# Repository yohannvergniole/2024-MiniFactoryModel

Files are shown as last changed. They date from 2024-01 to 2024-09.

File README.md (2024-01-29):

# Mini Factory Project

Template pour la création d'un repo type projet pour le MakerSpace. Doc gérée via le thème [Just-The-Docs](https://just-the-docs.com) en vanilla.

## Bienvenue sur Notre Projet

Ce repository est le cœur de notre projet. Ici, vous trouverez toutes les ressources nécessaires pour comprendre, utiliser et contribuer à notre projet.

### Contenu du Repository

- **Documentation :** Toutes les documentations techniques et guides d'utilisation sont disponibles dans le dossier `docs`. Voir le site de doc associé. 
- **project :** Toutes les sources de notre projet.

### Comment Utiliser ce Repository ?

- Pour commencer, consultez la documentation dans le dossier `docs`.
- Si vous souhaitez contribuer au projet, veuillez lire nos directives de contribution.

## Contribution

Nous accueillons et apprécions toute contribution. Si vous souhaitez contribuer, veuillez consulter notre guide de contribution pour connaître nos attentes et notre processus.

## Contact

Si vous avez des questions ou des suggestions, n'hésitez pas à nous contacter.

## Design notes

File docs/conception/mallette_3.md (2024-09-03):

---
layout: default
nav_order: 2
title: mallette 3
parent: Conception et prototypage
---

# Mallette 3

## Croquis

<script type="module" src="https://ajax.googleapis.com/ajax/libs/model-viewer/3.4.0/model-viewer.min.js"></script>

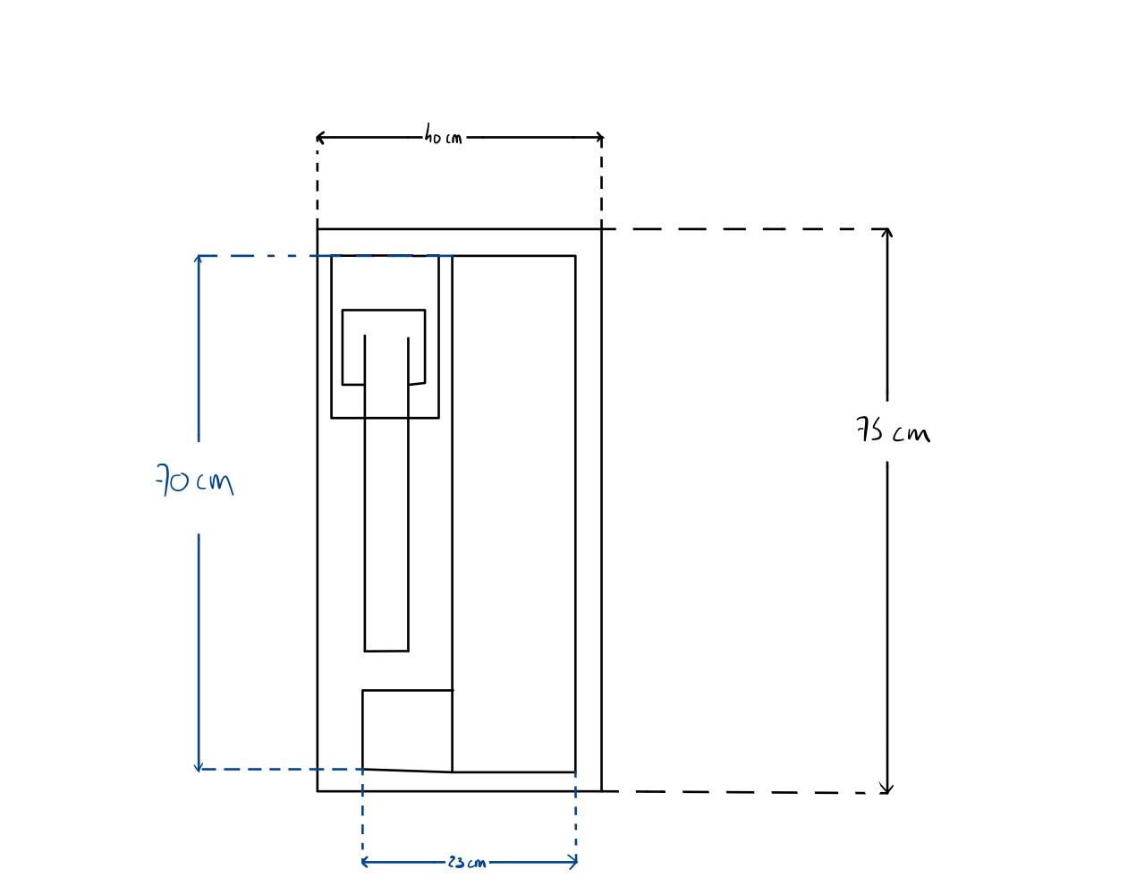
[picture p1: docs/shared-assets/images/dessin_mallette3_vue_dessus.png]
Plan de la mallette

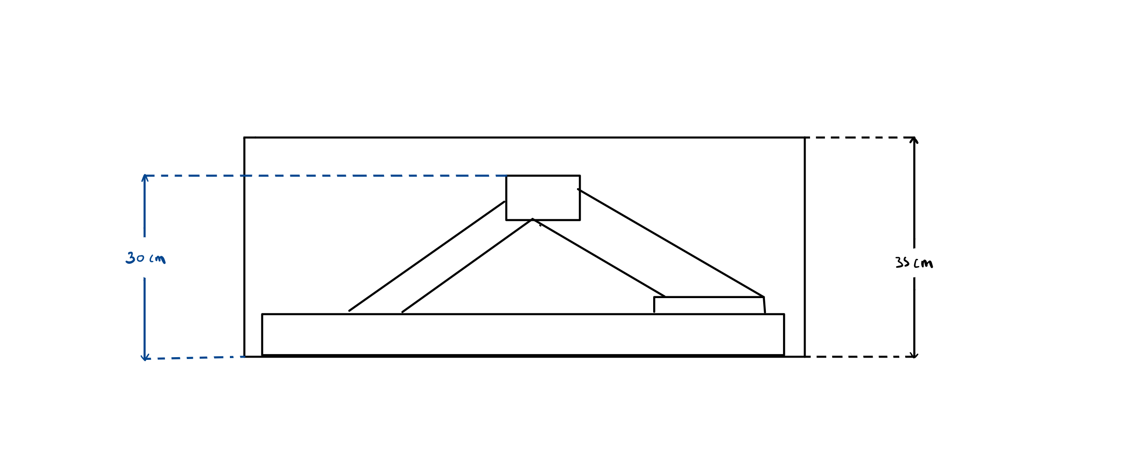
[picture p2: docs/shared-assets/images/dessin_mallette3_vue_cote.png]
Plan de la mallette

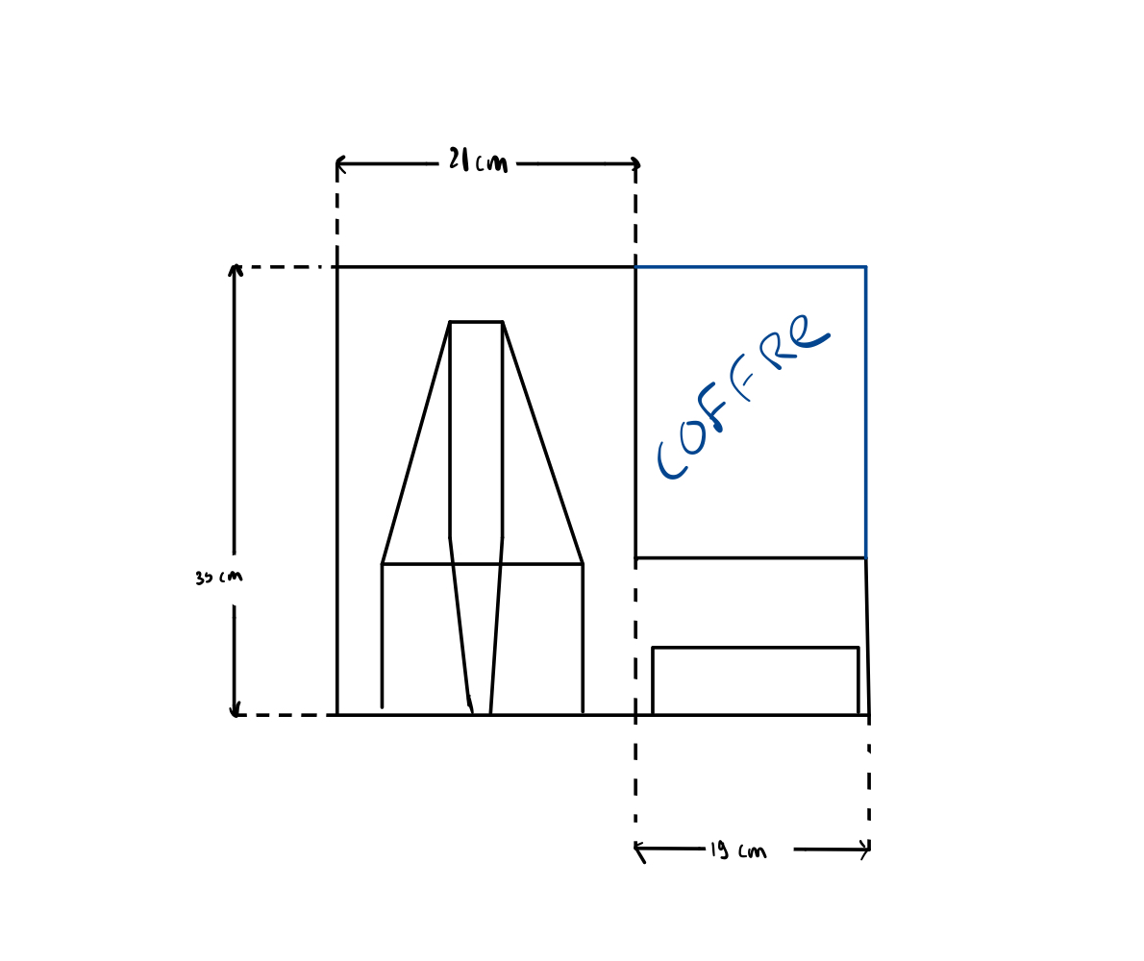
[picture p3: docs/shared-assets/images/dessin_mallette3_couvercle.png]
Plan de la mallette


---

## Modèle 3D

<model-viewer
    id="viewer"
    alt="Modèle 3D du bras robot Niryo Ned 2"
    src="../shared-assets/models/3D_REPRESENTATION.gltf"
    poster="../shared-assets/images/3D_REPRESENTATION.png"
    shadow-intensity="1"
    camera-controls
    touch-action="pan-z"
    rotation="0 0 90">
</model-viewer>

---

## Prototypage

Nous avons réalisé un prototype à l'échelle 1/10 des dimensions souhaitées pour le prototype final.
Ce prototype nous permettra d'éviter des erreurs futures lors de la conception. En effet, on a constaté qu'il manquait les coins sur les longueurs de la boîte.
On ajustera donc les dimensions du prototype final pour pouvoir obtenir un rectangle régulier.
Seul un côté restera sans coin, celui de la liaison des deux parties du socle puisque celles-ci doivent pouvoir s'aligner côte à côte.

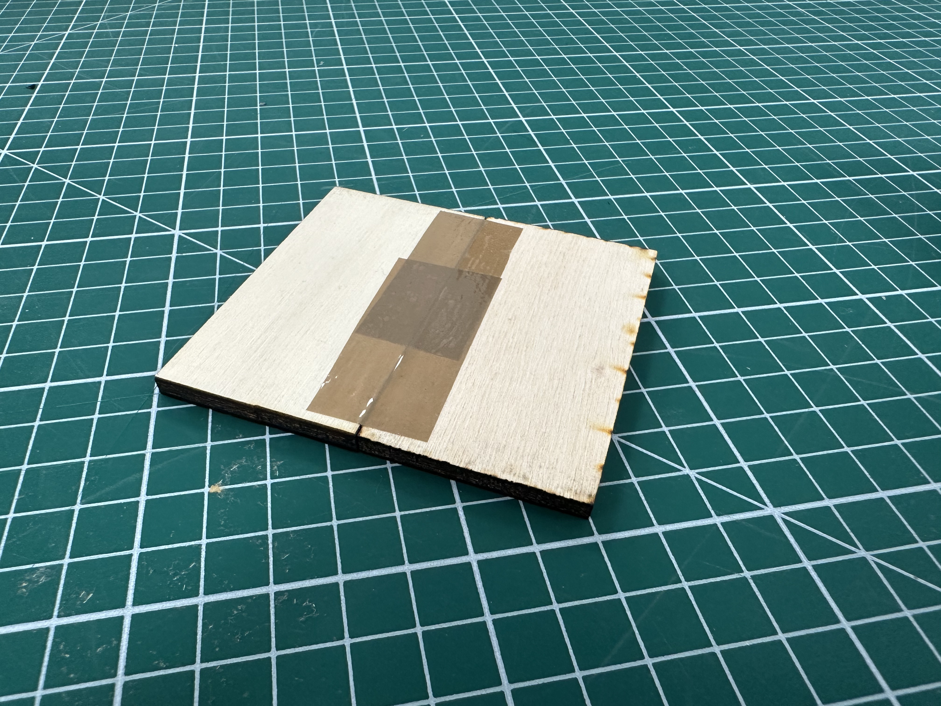
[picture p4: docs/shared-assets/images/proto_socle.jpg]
Photo socle

Photo du socle déplié, le scotch représente la charnière permettant la rotation des deux parties.

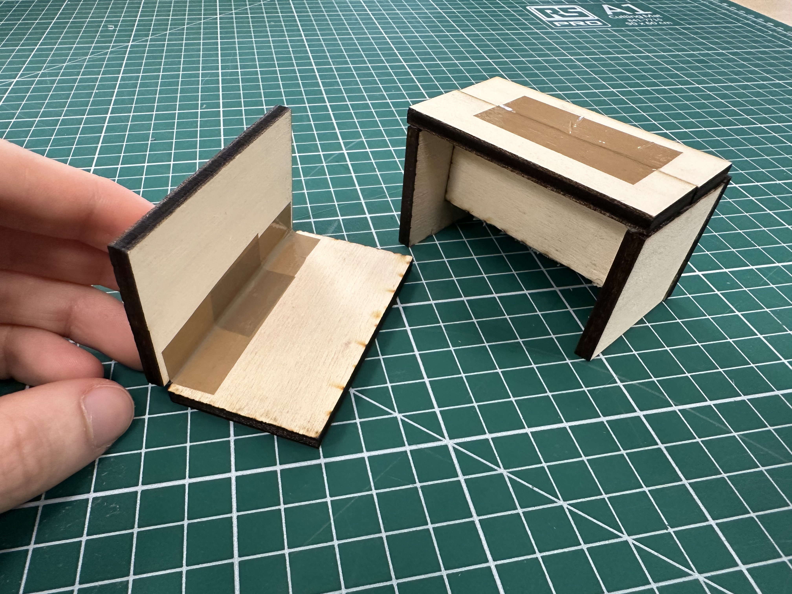
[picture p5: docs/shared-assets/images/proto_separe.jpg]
Photo socle et couvercle

Photo du socle et du couvercle séparé.

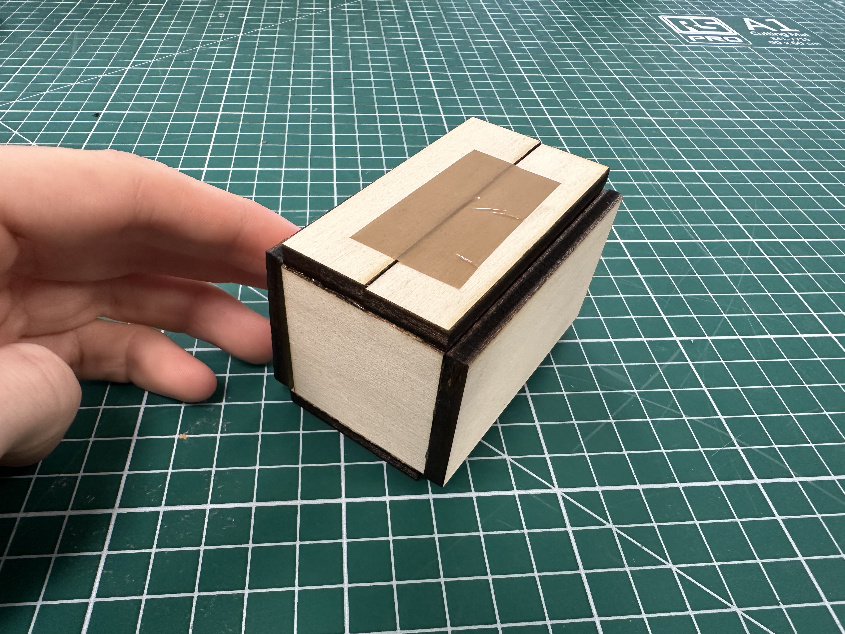
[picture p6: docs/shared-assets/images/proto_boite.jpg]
Photo boite

Photo de la boîte fermée lorsque le couvercle est posé sur le socle. Sur ce prototype, rien ne permet d'attacher le socle et le couvercle ensemble mais sur le prototype final ce sera fait grâce à des [sauterelles](../conception/supportCharniere.md).

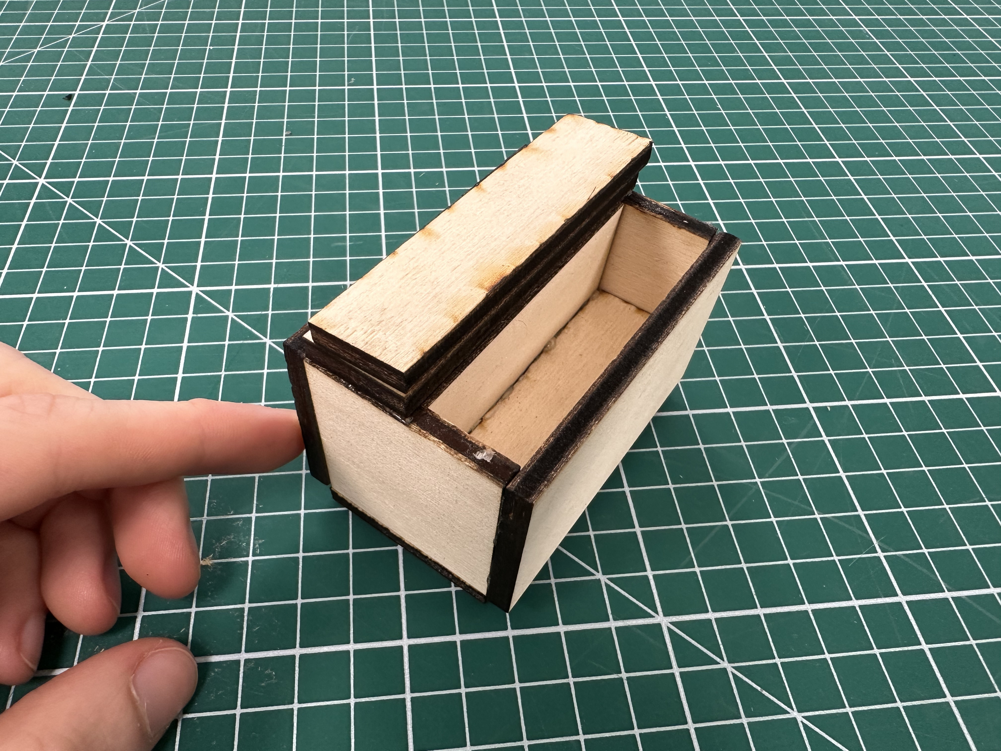
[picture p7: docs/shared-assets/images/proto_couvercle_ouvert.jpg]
Photo couvercle ouvert

Photo de la boîte avec le couvercle du coffre ouvert, ici aussi le scotch fais office de charnière.

<style>
    #viewer
    {
        margin : auto;
        width : 500px;
        height : 500px;
    }
</style>

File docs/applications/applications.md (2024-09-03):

---
layout: default
nav_order: 5
title: Modules
has_children: true
---

# Les différentes applications possibles avec notre Projet

Nous avons deux applications différentes.

La première est la simulation d'une chaîne de tri. Pour cette utilisation, nous pouvons utiliser un tri selon les couleurs et les formes. Il y a aussi la possibilité de choisir la couleur et la forme que nous souhaitons garder. [(voir page Module Chaine de Tri)](chaineTri.md)

La seconde est la prise d'un objet à un endroit précis et son transfert sur le convoyeur. [(voir page Module Transfert)](transfert.md)

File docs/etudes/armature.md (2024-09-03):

---
layout: default
nav_order: 7
title: Armature de la boîte
parent: Études et choix techniques
---
<script type="module" src="https://ajax.googleapis.com/ajax/libs/model-viewer/3.4.0/model-viewer.min.js"></script>

# Pourquoi une armature ?

Nous avons comme contrainte d'utiliser la découpeuse laser de l'école afin de réaliser notre mallette en planche de peuplier de 5mm. Cependant, avec la masse importante de matériel se trouvant dans la mallette, il est certain que des planches de 5mm ne suffieraient pas.
Nous avons étudié la possibilité de doubler l'épaisseur en réalisant la mallette avec deux couches de 5mm. La mallette était assez grande, cette possibilité nécessitait un nombre de planches conséquant. Pas le choix, nous avions besoin de trouver une alternative.
De cette conclusion résulte l'armature. En effet, une armature réalisé à partir de profilés de 20x20mm recouverte d'une planche de peuplier de 5mm semblait être la meilleure solution respectant nos contraintes.

<model-viewer
    id="viewer"
    alt="Modèle 3D de l'armature"
    src="../shared-assets/models/armature.gltf"
    poster="../shared-assets/images/capture_armature.png"
    shadow-intensity="1"
    camera-controls
    touch-action="pan-z"
    rotation="90 90 90">
</model-viewer>

<style>
    #viewer
    {
        margin : auto;
        width : 500px;
        height : 500px;
    }
</style>

Nous pouvons donc réaliser cette armature pour la base de la mallette ainsi que pour le côté accueillant le plateau des grilles modulaires. voir [mallette 3](../conception/mallette_3.html).

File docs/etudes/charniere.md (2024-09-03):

---
layout: default
nav_order: 8
title: Charnière
parent: Études et choix techniques
---

<script type="module" src="https://ajax.googleapis.com/ajax/libs/model-viewer/3.4.0/model-viewer.min.js"></script>

Étant donné que nous avons besoin qu'un côté de la mallette soit pliable, nous avons besoin d'un mécanisme permettant de le faire. Nous avons donc opté pour une charnière piano sur toute la longueur de la mallette.

<model-viewer
    class="viewer"
    alt="Modèle 3D de l'armature"
    src="../shared-assets/models/hinge.gltf"
    poster="../shared-assets/images/capture_charniere.png"
    shadow-intensity="1"
    camera-controls
    touch-action="pan-z"
    rotation="90 90 90">
</model-viewer>

<style>
    .viewer
    {
        margin : auto;
        width : 500px;
        height : 500px;
    }
</style>

Nous pouvons ainsi la fixer sur notre mallette. Cependant, cette charnière nous inflige une nouvelle contrainte. En effet, à cause de celle-ci, nous ne pouvons pas fixer notre armature sur les bords de nos planches de peuplier : les profilés faisant 20mm et la charnière faisant 32mm (donc 16mm de chaque côté), il est impossible de fixer notre charnière sur nos planches. Nous avons donc décider de décaler l'armature comme ceci :
<model-viewer
    class="viewer"
    alt="Modèle 3D de l'armature"
    src="../shared-assets/models/problemeCharniere.gltf"
    poster="../shared-assets/images/problemeCharniere.png"
    shadow-intensity="1"
    camera-controls
    touch-action="pan-z"
    rotation="90 90 90">
</model-viewer>

Malheureusement pour nous, ceci créé un autre problème. Visser la charnière seulement dans une plaque de 5mm met en péril la solidité de la structure. Nous avons donc besoin d'une [pièce de support](../realisation/ressources.md#les-profilés) dans laquelle nous allons visser la charnière.

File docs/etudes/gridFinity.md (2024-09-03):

---
layout: default
nav_order: 4
title: Projet Gridfinity
parent: Études et choix techniques
---

# Projet GridFinity

Le projet GridFinity est un système de rangement générique à imprimer en 3D. Il permet à n'importe qui de créer sa structure de rangement selon ses propres besoins.
Le principe est simple et similaire à celui des legos, on modélise des blocs de différentes tailles basés sur le même pattern afin de les emboîter facilement.
Voici des exemples afin de mieux comprendre le principe :

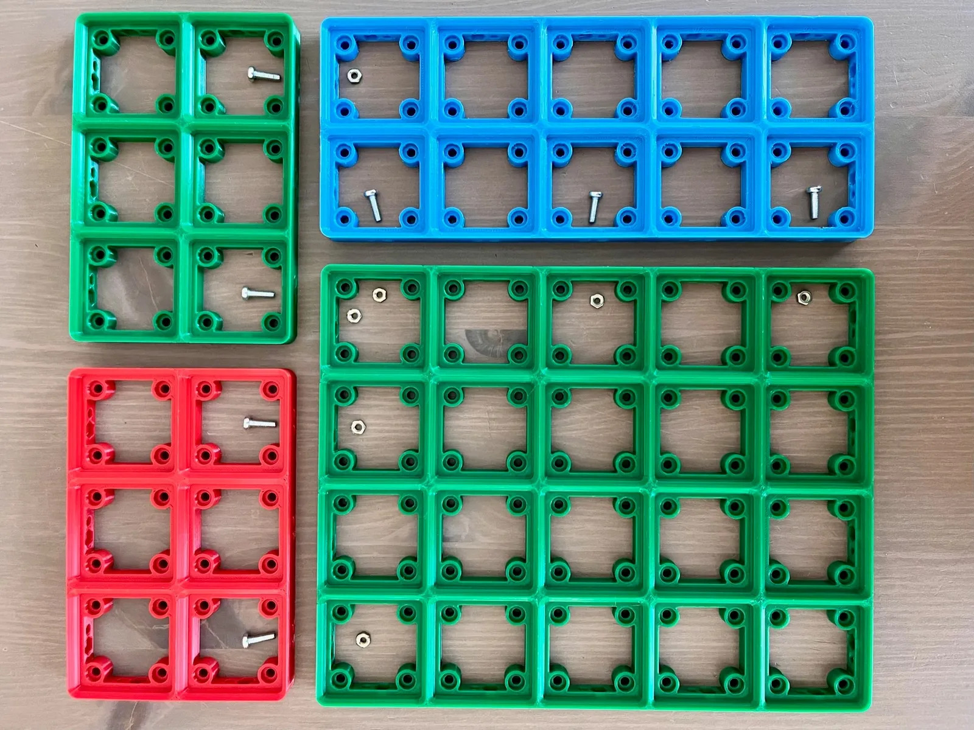
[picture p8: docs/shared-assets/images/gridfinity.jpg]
Illustration du projet gidfinity

*Sources :*
*[https://www.printables.com/fr/model/500544-gridfinity-baseplate-screwable/user-gcodes](https://www.printables.com/fr/model/500544-gridfinity-baseplate-screwable/user-gcodes)*

*[https://gridfinity.xyz](https://gridfinity.xyz)*

## Utilisation dans notre projet

Nous voulons utiliser ce système dans notre projet afin de faciliter la modularité. Ce système nous offre de nombreuses possibilités comme le fait de faire un plateau à coordonnées par exemple.

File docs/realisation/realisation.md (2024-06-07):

---
layout: default
title: Réalisation
nav_order: 7
has_children: true
---

# Étapes de Réalisation

Bienvenue dans la section dédiée aux étapes de fabrication du projet mini usine. Ici, vous trouverez des guides détaillés pour chaque étape du processus de fabrication.

## Sommaire des Étapes

Le processus de fabrication est divisé en plusieurs étapes clés :

1. [Choix des matériaux](ressources.md)
2. [Assemblage](assemblage.md)

---

Pour toute question ou aide supplémentaire, n'hésitez pas à contacter notre équipe.

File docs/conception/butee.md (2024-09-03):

---
layout: default
nav_order: 3
title: Butée 
parent: Conception et prototypage
---

## Première tentative

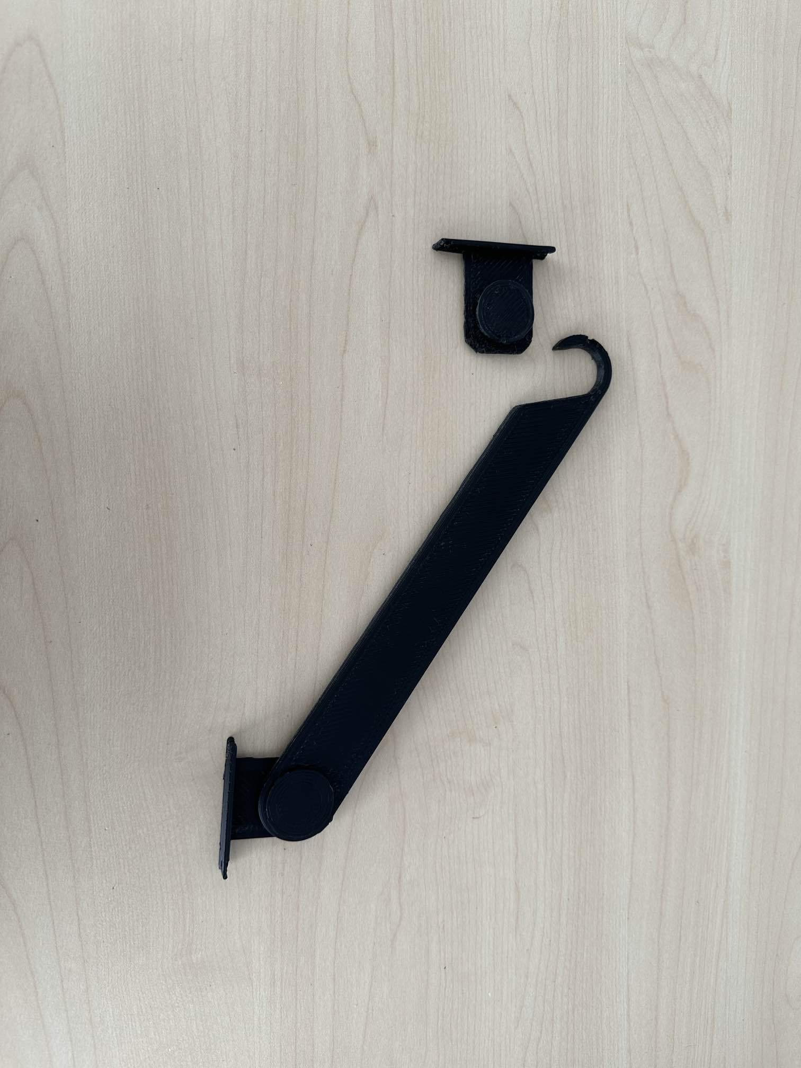
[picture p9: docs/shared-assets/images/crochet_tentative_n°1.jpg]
Illustration crochet tentative n°1


Notre crochet était malheureusement trop long pour qu'il puisse se glisser sur le support que l'on peut voir sur l'image ci-dessus.
De plus, certaines liaisons n'ont pas été parfaitement dimensionnées, nous avonc dû ajuster le tir sur la seconde tentative afin d'obtenir un glissement parfait et un bon maintien des cotés de la mallette lors de sa fermeture par le biais des crochets.

## Seconde tentative

Illustration crochet tentative finale

Sur cette itération finale, nous avons pris la décision de faire un crochet allongé avec un creux parrallèle à la plaque inférieure de la mallette afin de faciliter l'emboîtement des deux pièces tout en s'assurant du maintien de la plaque latérale.

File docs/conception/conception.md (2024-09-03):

---
layout: default
nav_order: 6
title: Conception et prototypage
has_children: true
---

# Conception et prototypage

Nous avons imaginé 3 possibilités pour réaliser notre projet.
Ci-dessous nous vous présentons les modèles 3D des différentes idées en expliquant pour chaque leurs avantages et leurs inconvénients.

## Mallette 1

<script type="module" src="https://ajax.googleapis.com/ajax/libs/model-viewer/3.4.0/model-viewer.min.js"></script>

<model-viewer
    id="viewer"
    alt="Modèle 3D du bras robot Niryo Ned 2"
    src="../shared-assets/models/mallette_1.gltf"
    poster="../shared-assets/images/capture_niryo.jpg"
    shadow-intensity="1"
    camera-controls
    touch-action="pan-z"
    rotation="0 0 90">
</model-viewer>

<style>
    #viewer
    {
        margin : auto;
        width : 500px;
        height : 500px;
    }
</style>

| Avantages | Inconvénients |
| :---: | :---: |
| Tout est contenu dans la boîte  | Volumineuse |
|  | Transport |

## Mallette 2

<model-viewer 
    id="viewer"
    alt="Modèle 3D du bras robot Niryo Ned 2"
    src="../shared-assets/models/mallette_2.gltf"
    poster="../shared-assets/images/capture_niryo.jpg"
    shadow-intensity="1"
    camera-controls
    touch-action="pan-z"
    rotation="0 0 90">
</model-viewer>

| Avantages | Inconvénients |
| :---: | :---: |
| Tout est contenu dans la boîte  | Instable |
|  | Descente du bras robot restreinte |

## Mallette 3

<model-viewer
    id="viewer"
    alt="Modèle 3D du bras robot Niryo Ned 2"
    src="../shared-assets/models/3D_REPRESENTATION.gltf"
    poster="../shared-assets/images/3D_REPRESENTATION.png"
    shadow-intensity="1"
    camera-controls
    touch-action="pan-z"
    rotation="0 0 90">
</model-viewer>

| Avantages | Inconvénients |
| :---: | :---: |
| Tout est contenu dans la boîte  | Encombrant à transporter |
| Plan de travail réduit |  |

C'est ce choix que nous avons décidé de réaliser.

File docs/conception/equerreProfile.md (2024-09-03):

---
layout: default
nav_order: 5
title: Equerre Profilés
parent: Conception et prototypage
---

L'équerre pour profilé a été modélisée et imprimée en 3D pour assurer le maintien de l'armature réalisée avec les profilés.
Nous avons décidé de les réaliser nous-mêmes pour gagner du temps et limiter les dépenses, car une équerre en impression 3D coûte moins cher qu'une réalisée en métal.

<script type="module" src="https://ajax.googleapis.com/ajax/libs/model-viewer/3.4.0/model-viewer.min.js"></script>

<model-viewer
    id="viewer"
    alt="Modèle 3D du bras robot Niryo Ned 2"
    src="../shared-assets/models/equerreFixe.gltf"
    poster="../shared-assets/images/equerreFixe.png"
    shadow-intensity="1"
    camera-controls
    touch-action="pan-z"
    rotation="90 90 90">
</model-viewer>

<style>
    #viewer
    {
        margin : auto;
        width : 500px;
        height : 500px;
    }
</style>

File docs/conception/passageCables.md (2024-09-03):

---
layout: default
nav_order: 6
title: Passage de  Câbles
parent: Conception et prototypage
---
<script type="module" src="https://ajax.googleapis.com/ajax/libs/model-viewer/3.4.0/model-viewer.min.js"></script>

Afin d'organiser l'espace de travail de notre mini usine, nous avons décidé de réaliser des passages de câbles. Cela évite que le robot ne s'emmêle dans les câbles et nous permet en même temps d'avoir un espace de travail rangé et agréables à utiliser.
Cette pièce montre également l'étendue des possibilités que nous avons grâce à la grille modulaire.

<model-viewer 
    id="viewer" 
    alt="Support Charnière" 
    src="../shared-assets/models/passageCables.gltf" 
    poster="../shared-assets/images/passageCables.png" 
    shadow-intensity="1" 
    camera-controls 
    touch-action="pan-z"
    rotation="90 90 90">
</model-viewer>

<style>
    #viewer
    {
        margin : auto;
        width : 500px;
        height : 500px;
    }
</style>

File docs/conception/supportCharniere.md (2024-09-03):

---
layout: default
nav_order: 4
title: Support de la charnière
parent: Conception et prototypage
---

Ce support modélisé en 3D permet de fixer la charnière au socle.
Nous avons réalisé une pièce qui se glisse dans le profilé, ce qui facilite la fixation nécessitant une vis et un écrou. Nous l'avons modélisé en 3D car nous voulions une forme spécifique pour notre projet, non disponible sur le marché.

<script type="module" src="https://ajax.googleapis.com/ajax/libs/model-viewer/3.4.0/model-viewer.min.js"></script>

<model-viewer 
    id="viewer" 
    alt="Support Charnière" 
    src="../shared-assets/models/SUP_CHARNIERE.gltf" 
    poster="../shared-assets/images/SUP_CHARNIERE.png" 
    shadow-intensity="1" 
    camera-controls 
    touch-action="pan-z"
    rotation="90 90 90">
</model-viewer>

<style>
    #viewer
    {
        margin : auto;
        width : 500px;
        height : 500px;
    }
</style>

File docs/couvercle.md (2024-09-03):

---
layout: default
nav_order: 10 
title: Modèle 3D du couvercle
---

<script type="module" src="https://ajax.googleapis.com/ajax/libs/model-viewer/3.4.0/model-viewer.min.js"></script>

# Modèle 3D du couvercle

Nous avons modélisé le couvercle, si vous souhaitez le réaliser vous pouvez voir un aperçu ci-dessous. 
Le fichier est disponible dans les ressources du site.

<model-viewer
    id="viewer"
    alt="Modèle 3D du couvercle"
    src="../shared-assets/models/couvercle.gltf"
    poster="../shared-assets/images/couvercle.png"
    shadow-intensity="1"
    camera-controls
    touch-action="pan-z"
    rotation="90 90 90">
</model-viewer>

<style>
    #viewer
    {
        margin : auto;
        width : 500px;
        height : 500px;
    }
</style>

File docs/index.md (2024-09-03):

---
layout: home
nav_order: 1
title: Accueil
---

# Bienvenue sur notre documentation du projet Mini Factory

Bienvenue dans la documentation du projet Mini Factory Model. Ce site a pour but de fournir toutes les informations nécessaires pour comprendre, utiliser et reproduire efficacement notre projet.

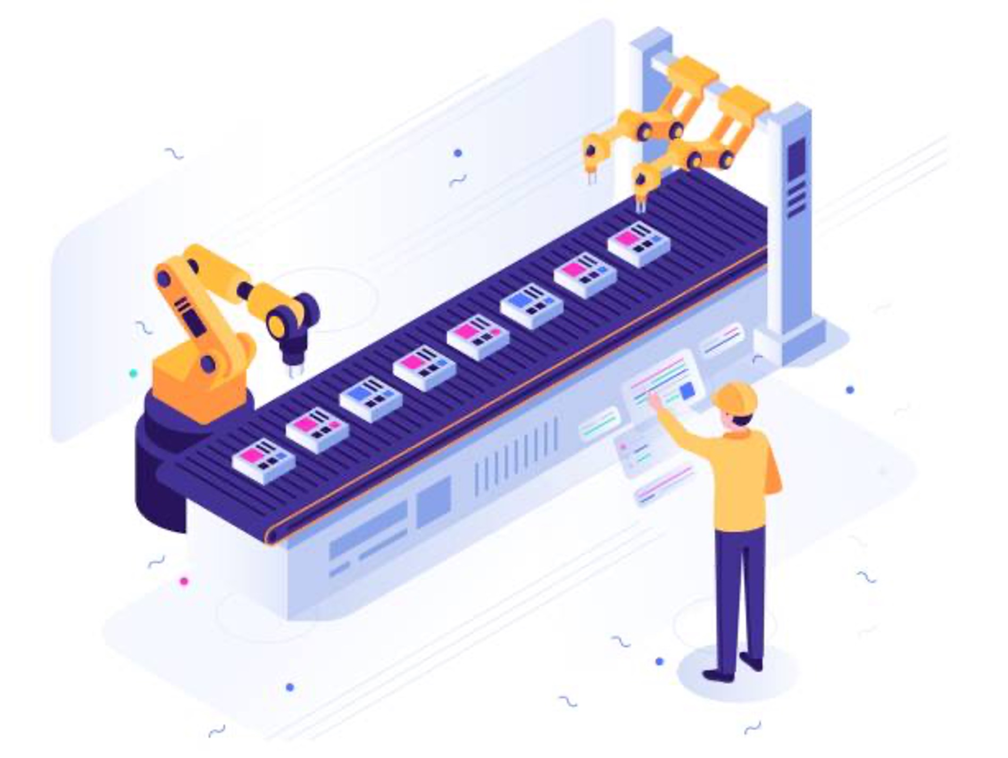
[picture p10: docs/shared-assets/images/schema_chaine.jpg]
Illustration montrant un schéma d'une chaîne représantant notre projet de maquette d'intéraction sur des objets présent sur un convoyeur


## À propos du Projet

Le but principal de la chaîne de production est de trier des objets en fonction des formes et/ou des couleurs en utilisant le bras robotisé.

Le but de notre projet est de réaliser une maquette de chaîne de tri transportable vers diverses lieux. En effet, Unilasalle Amiens possède une filière PAUC (Production Automatisée et Usine Connectée) et un tel projet, pourrait permettre de faire la promotion de cette filière ou simplement de faire découvrir l’univers de l'industrie et de la production automatisée.

## Poster

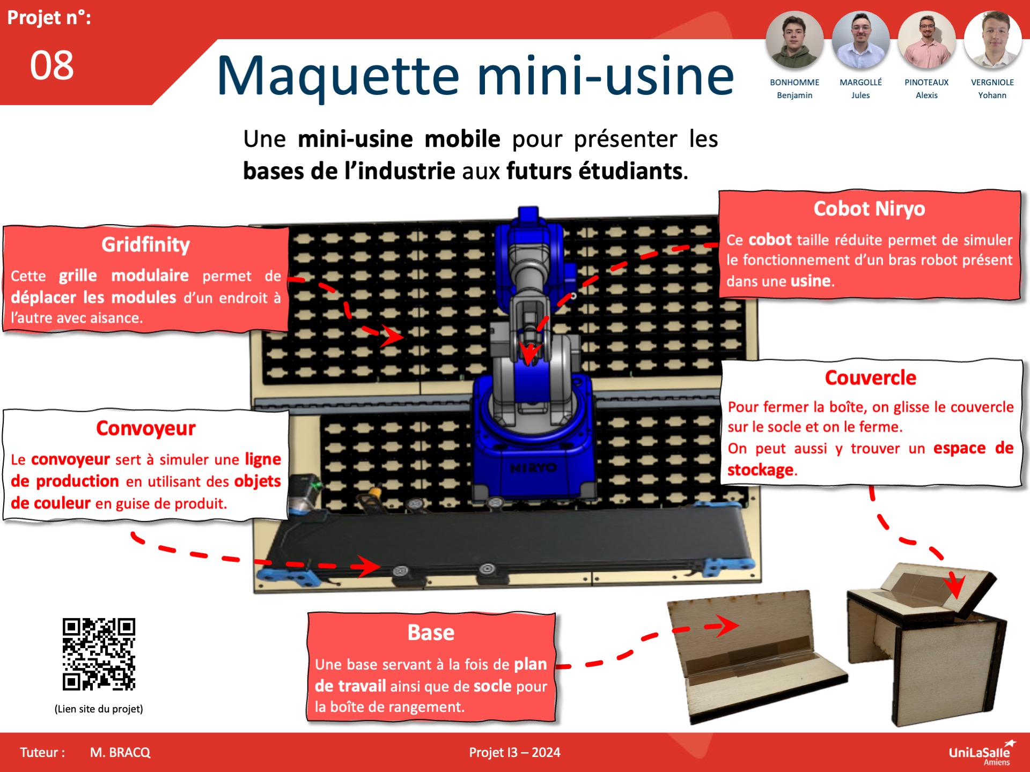
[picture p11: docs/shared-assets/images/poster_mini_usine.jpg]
photo poster


## Vidéo

<iframe width="100%" height="500" src="https://www.youtube.com/embed/1ccF_rse7Ak" frameborder="0" allow="accelerometer; autoplay; encrypted-media; gyroscope; picture-in-picture" allowfullscreen></iframe>

---

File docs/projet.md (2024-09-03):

---
layout: default
nav_order: 3 
title: Présentation du projet
---

# Présentation du projet

## Introduction

Dans le cadre de notre projet I3, nous avons à réaliser un projet sur 75h de cours sans compter le temps personnel à investir. Ce projet à pour objectif de développer le travail en équipe sur des sujets en cohérence avec les études et les compétences que l'on souhaite développer ultérieurement.

## Contexte du Projet

Plusieurs sorties promotionnelles sont organisées par le pôle communication de l'école dans les alentours d'Amiens afin d'attirer de nouveaux élèves. Celles-ci ont pour objectif de promouvoir au mieux les compétences développées au sein de l'école de manière simple et ludique. Notre projet est né de ce postulat de base, la nécessité de créer un support visuel et physique qui puisse exposer du mieux possible les connaissances et l'expertise transmisent dans notre cursus scolaire.

## Objectifs du Projet

Nous nous sommes orientés sur ce projet dans le but de fournir une maquette/chaîne robotique de production concrète miniaturisée et transportable. Celle-ci a comme objectif d'être facile à prendre en main et à installer pour l'utilisateur et pour ceux qui observent. Cette chaine de production sera modulable afin de promouvoir la polyvalence de l'enseignement avec une maquette multi-usage.

## Cahier des Charges

[https://cloudlasalle-my.sharepoint.com/:x:/g/personal/alexis_pinoteaux_etu_unilasalle_fr/Ee9_swYYa1JEvp3mi1WHuzgBoHQftADFWFV2qyiBQeqNow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)](https://cloudlasalle-my.sharepoint.com/:x:/g/personal/alexis_pinoteaux_etu_unilasalle_fr/Ee9_swYYa1JEvp3mi1WHuzgBoHQftADFWFV2qyiBQeqNow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)

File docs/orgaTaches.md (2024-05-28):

---
layout: default
nav_order: 9 
title: Organisation des Tâches
---
# Organisation des Tâches

Afin d'organiser notre travail, nous avons choisi de créer un tableau Trello utilisant la méthode Kanban. Cette méthode nous permet une bonne visualisation des tâches à effectuer et facilite la répartition.

<embed type="text/html" src="https://trello.com/b/otUl7l00.html" width="800" height="600">
[Lien vers le Trello](https://trello.com/b/otUl7l00/mini-factory)

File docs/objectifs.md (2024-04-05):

---
layout: default
nav_order: 2
title: Maquette de chaîne de production 
---

# Introduction

Dans le cadre de notre projet I3, nous avons à réaliser un projet sur 75h de cours sans compter le temps personnel à investir pour développer le travail en équipe sur des sujets en cohérence avec les études et les compétences que l'on souhaite développer ultérieurement.

# Contexte du Projet

Plusieurs sorties promotionnelles sont organisées par le pôle communication de l'école dans les alentours d'amiens afin d'attirer de nouveaux élèves. Celles-ci ont pour objectif de promouvoir au mieux les compétences développées au sein de l'école de manière simple et ludique. Notre projet est né de ce postulat de base, la nécessité de créer un support visuel et physique qui puisse exposé du mieux possible les connaissances et l'expertise transmise dans notre cursus scolaire.

# Objectifs du Projet

Nous nous sommes orientés sur ce projet dans le but de fournir une maquette/chaîne robotique de production concrète miniaturisée et transportable. Celle-ci a comme objectif d'être facile à prendre en main et à installer pour l'utilisateur et pour ceux qui observent. Cette chaine de production sera modulable afin de promouvoir la polyvalence de l'enseignement avec une maquette multi-usage.

# Existant

Nous avons repris l'idée originale de ce projet qui a été trouvée lors du projet I2 sur un autre bras. Pour parvenir à un résultat concluant, nous partons d'un bras robotisé le ned 2 qui est fourni par l'école au début de ce projet avec ses accessoires.

# Cahier des Charges

[https://cloudlasalle-my.sharepoint.com/:x:/g/personal/alexis_pinoteaux_etu_unilasalle_fr/Ee9_swYYa1JEvp3mi1WHuzgBoHQftADFWFV2qyiBQeqNow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)](https://cloudlasalle-my.sharepoint.com/:x:/g/personal/alexis_pinoteaux_etu_unilasalle_fr/Ee9_swYYa1JEvp3mi1WHuzgBoHQftADFWFV2qyiBQeqNow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)

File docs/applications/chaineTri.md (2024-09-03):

---
layout: default
nav_order: 2
title: Module Chaine de tri
parent: Modules
---

# Chaîne de Tri

Cette application est la première idée que nous avons eu en commençant le projet.

## Fonctionnement

L'utilisateur doit d'abord placer le robot à l'emplacement lié à la démonstration comme ci-dessous.

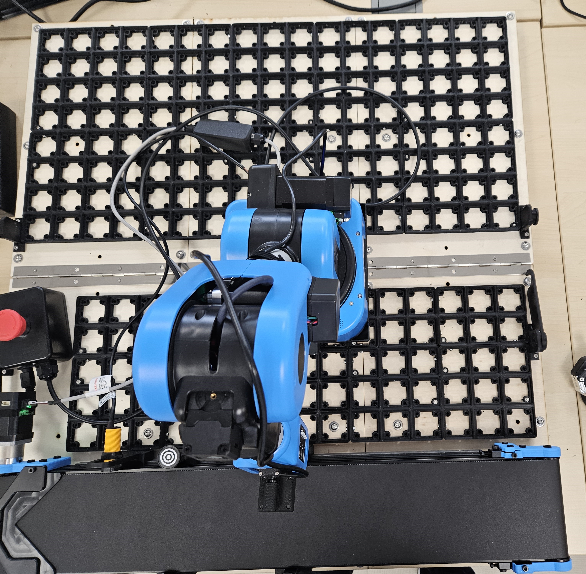
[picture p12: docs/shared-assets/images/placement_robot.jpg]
photos montrant le placement robot


Par la suite, il faut placer les 3 plaques qui recevront les objets triés.

## Matériel

Pour ce module, nous avons besoin :

- Un convoyeur qui va amener les objets au bras robot
- Le bras robot
- Des capteurs pour la couleur et la forme des objets
- Des plaques pour recevoir les objets triés

## Le kit Vision de Niryo

Niryo met en vente beaucoup d'accessoires pouvant compléter le bras robot, parmi ceux-ci, nous retrouvons le kit Vision.

animation gif du kit vision de niryo

<br>

Le kit Vision nous permet de faire de la reconnaissance de forme et de couleur, parfait pour notre module.
Nous utiliserons uniquement les trois couleurs des objets fournis (rouge, vert et bleu) ainsi que leurs deux formes utilisées (rond et carré).
Le kit vision comprend :

- Une zone de travail
- Une caméra
- Des objets à manipuler
- Une pointe de précision

La zone de travail est une zone créée par 4 "balises" permettant à la caméra de se repérer.

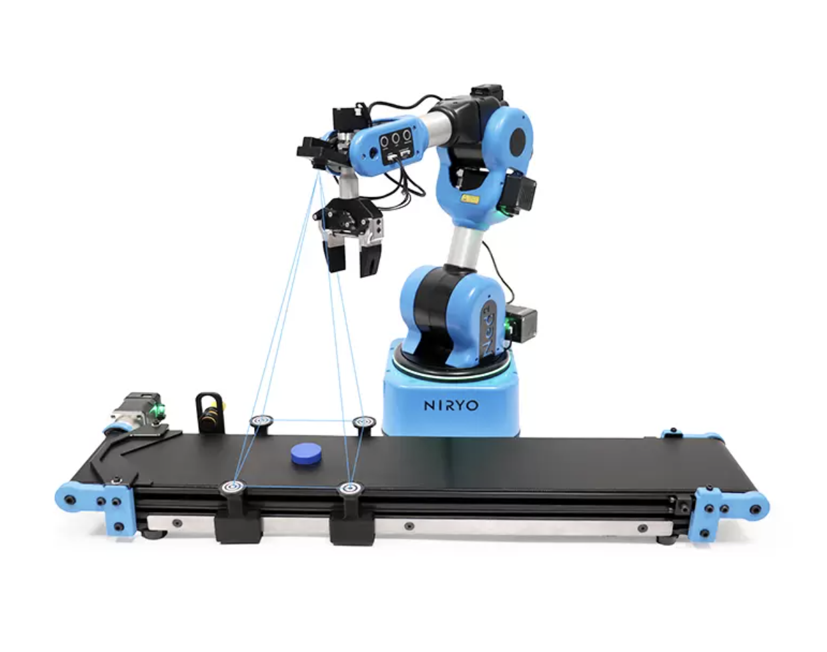
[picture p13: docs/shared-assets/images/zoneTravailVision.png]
image de la zone de travail du kit vision


## Et après le tri ?

L'utilisateur renseigne donc la façon dont il veut trier ses objets et le bras fait tout le reste. Les objets lui sont amenés via un convoyeur et il les range ensuite dans leur boîte attitrée.
Par exemple, si l'utilisateur veut trier les objets par couleur et ne garder que la couleur <span style="color:green;">verte</span>, alors il aura besoin de deux contenant : un pour les objets verts, et un pour le reste.

*Source : https://niryo.com/fr/produits-cobots/ensemble-de-vision-ned2/*

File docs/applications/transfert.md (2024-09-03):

---
layout: default
nav_order: 3
title: Module Transfert 
parent: Modules
---

# Transfert de prièce

## Fonctionnement

L'utilisateur doit d'abord placer le robot à l'emplacement lié à la démonstration comme ci-dessous.

photos montrant le placement robot

Par la suite, il faut placer la plaque qui recevra les objets à transporter.

Une fois le programme lancé, les objets devront être placés les uns après les autres pendant l'execution du programme. Il faut faire attention à bien placer la pièce au centre de la plaque.

## Matériel

Pour ce module, nous avons besoin :

- Un convoyeur qui va amener les objets au bras robot
- Le bras robot
- Une plaque pour prendre les objets

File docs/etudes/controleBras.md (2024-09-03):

---
layout: default
nav_order: 6
title: Contrôle du Bras
parent: Études et choix techniques
---

# Comment contrôler le bras Niryo ?

Nous pouvons contrôler le bras robot grâce à un logiciel disponible gratuitement et conçu spécialement pour l'utilisation du bras.

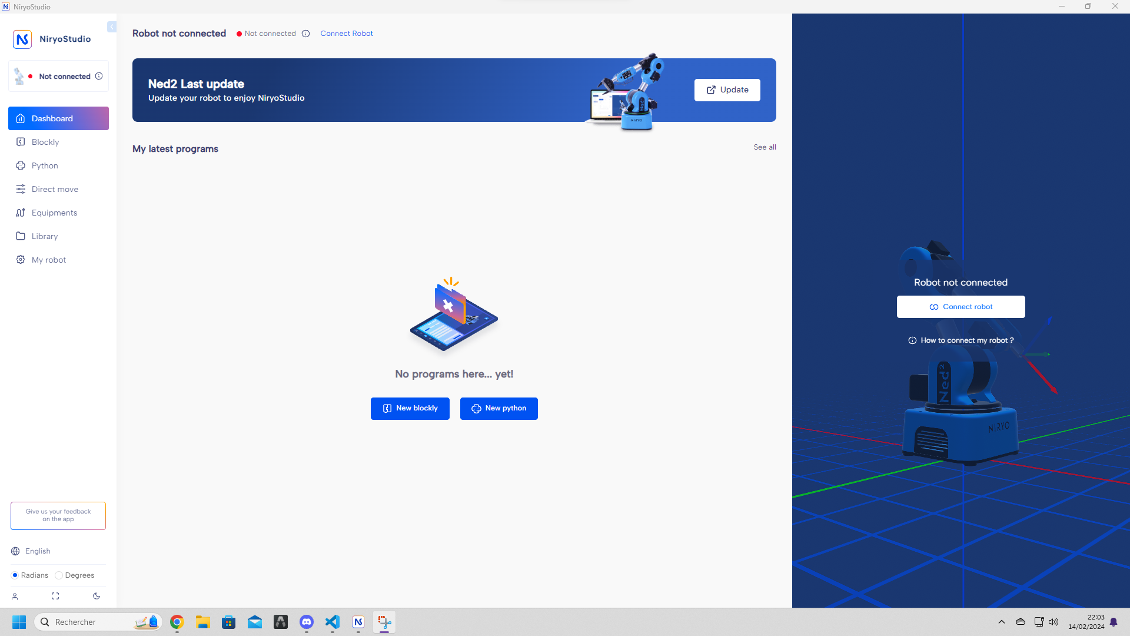
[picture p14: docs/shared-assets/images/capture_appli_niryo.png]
Capture d'écran de l'application Niryo


Cette application a été conçu pour faciliter l'utilisation et la configuration du bras Niryo.
Il est possible de le programmer avec le langage *Blockly* qui est un langage d'assemblage de blocs.

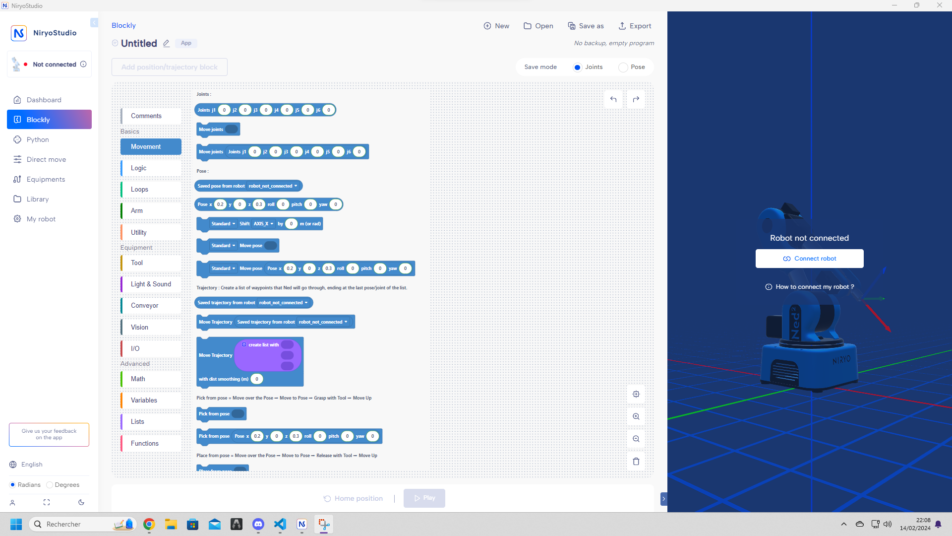
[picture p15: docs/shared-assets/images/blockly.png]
Capture d'écran de l'application Niryo affichant le langage blockly


Le robot est également configurable, via l'application, avec le langage python.

## Quelle solution allons-nous choisir ?

Nous pensons que l'utilsation du langage *Blockly* est la meilleure option pour nous. En effet, notre projet doit être une solution éducative et facile à mettre en place pour des utilisateurs qui ne s'y connaissent pas énormément. Blockly est un langage facile à prendre en main et ressemble beaucoup à Scratch qui est un langage qui est étudié dans beaucoup de collèges.

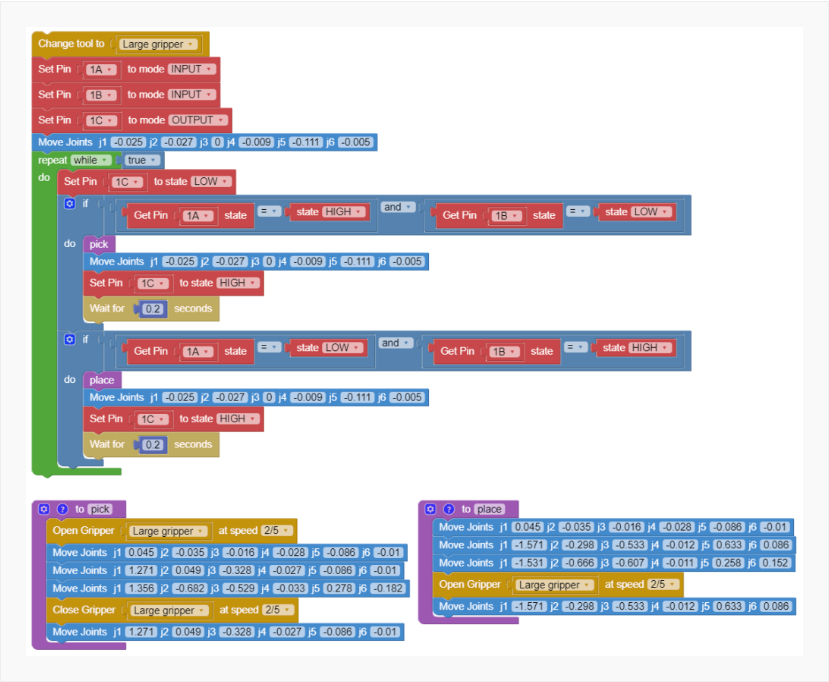
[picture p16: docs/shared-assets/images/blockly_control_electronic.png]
illustration controle niryo avec une carte électronique


*Source : [https://docs.niryo.com/applications/ned/v1.0.3/en/source/tutorials/control_ned_arduino.html](https://docs.niryo.com/applications/ned/v1.0.3/en/source/tutorials/control_ned_arduino.html)*

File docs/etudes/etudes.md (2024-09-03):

---
layout: default
nav_order: 4
title: Études et choix techniques
has_children: true
---

# Études et choix techniques

Sur cette page, nous répertorions toutes les prises de décisions techniques et les recherches qui nous ont permis de choisir la meilleure solution en fonction des informations à notre disponibilité.  

Tout au long de ce projet, plusieurs dilemmes apparaîtront afin de déterminer les pièces, les matériaux, le fonctionnement ainsi que l'agencement de notre chaîne de production. Pour parvenir à un choix voici les étapes par lesquelles nous passerons :

- Réflexion
- Recherches/Études des solutions existantes
- Explication du choix final (en fonction des conclusions des recherches)

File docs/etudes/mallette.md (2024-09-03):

---
layout: default
nav_order: 3
title: Mallette de Transport
parent: Études et choix techniques
---

# La Mallette

Afin que notre projet soit le plus facilement transportable nous avons pensé
que la création d'une mallette de transport contenant tout le nécessaire pour la
mise en place du projet serait la meilleure solution. Le but étant d'avoir une mallette que nous pouvons ouvrir, déplier sur une table et avoir le projet prêt à être utilisé.
La conception de cette mallette n'est pas si facile. En effet, nous avons besoin d'une mallette assez grande pour pouvoir y stocker le bras robot ainsi que le convoyeur et un ordinateur mais d'une taille raisonnable pour pouvoir être transportable.

## La conception

Nous avons eu plusieurs idées de conception (voir [conception](../conception/conception.html)) afin de répondre au mieux à nos attentes.
Nous allons maintenant procéder à la description du modèle, de ses atouts et de ses inconvénients pour chacune des mallettes.

## Modèle N°1

(voir [malette_1](../conception/mallette_1.html))

Le tout premier modèle sur lequel nous nous sommes entendus, est une mallette avec une architecture assez simple mais compact afin de prendre le moins d'espace lors du transport. Pour cela, nous avons opté pour une forme rectangulaire basique qui puisse comprendre tous les modules (voir [Modules](../applications/applications.html)), le convoyeur au centre de la mallette, l'ordinateur de commande et les objets annexes nécessaires au bon fonctionnement des modules. Pour ce prototype, nous avons fait le choix de ne pas y intégrer le robot Niryo (voir [Bras robotisé Niryo Ned 2 et ses accessoires](niryo.html)) afin de faciliter le transport de la mallette grâce à un poids restreint (le bras étant l'élément le plus lourd de la chaîne de production (7kg)) ainsi qu'une taille réduite.
De plus, il est très facile de déployer le dispositif grâce à sa forme géométrique simple qui une fois ouverte donne une chaîne dans la bonne disposition et prêt à l'utilisation.

Avantages :

- Forme simple et compact
- Poids faible
- Prise en main

Inconvénients :

- Robot à transporter à part
- Porter puis disposer le robot sur son emplacement établi
- Prise d'espace importante une fois déployé

## Modèle N°2

(voir [malette_2](../conception/mallette_2.html))

Notre second choix est une architecture plus complexe dans laquelle nous avons choisi d'y intégrer l'entièreté des composants de notre chaîne de production (le bras Niryo(voir [Bras robotisé Niryo Ned 2 et ses accessoires](niryo.html)), convoyeur,...). Nous avons imaginé un modèle à deux étages avec les modules dans l'un des tiroirs, dans le second le convoyeur et le bras robot placé sur la face supérieure du module.

Avantages :

- Toutes les pièces intégrées
- Rangement simplifié
- Espace de déploiement restreint

Inconvénients :

- Architecture complexe
- Faible stabilité
- Création difficile
- Poids élevé

## Modèle N°3

(voir [malette_3](../conception/mallette_3.html))

Notre troisième choix est la solution finale que nous avons réalisé. Cette solution combine les deux mallettes précédentes en intégrant la modularité de la première et le côté compacte de la seconde. Cette mallette ne prend pas beaucoup de place et permet de stocker tous les éléments nécessaire à l'intérieur. Cependant beaucoup de sujets sont à étudier pour permettre sa réalisation.

Avantages :

- Tout dedans
- Compact
- Rangements simplifiés
- Facilité d'utilisation
- Solidité accrue

Inconvénients :

- Repositionner le robot dans sa position initiale
- Poids élevé

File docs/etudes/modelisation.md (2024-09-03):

---
layout: default
nav_order: 10
title: Modélisation
parent: Études et choix techniques
---
<script type="module" src="https://ajax.googleapis.com/ajax/libs/model-viewer/3.4.0/model-viewer.min.js"></script>

Cette page sert à regrouper les différentes études concernant les modélisations 3D que nous avons réalisé.

## Butée

Afin de fermer la boîte, nous avons besoin d'un système qui permet de tenir celle-ci en angle droit afin de faciliter sa fermeture avec le couvercle. Nous avons donc modélisé un sytème de butée fixée à la boîte.
[butée](../conception/butee.html)

## Pièce de support pour la charnière

Pour pallier le problème de solidité au niveau de la charnière (voir [Charnière](charniere.html)) nous avons choisi de créer une pièce en modélisation 3D qui se fixera sur les profilés ainsi que sur la charnière.
Le but de cette pièce est de soulager la charnière. En effet, nous craignons que celle-ci, uniquement fixée dans une planche de 5mm, ne puisse pas supporter la masse qui lui sera appliquée. Nous avons donc conçu cette [pièce](../conception/supportCharniere.html).

## Equerre pour Profilés

Afin de fixer nos profilés ensemble, nous avons pensé à utiliser ce système :

<model-viewer
    id="viewer"
    alt="Modèle 3D du bras robot Niryo Ned 2"
    src="../shared-assets/models/equerreProfiles.gltf"
    poster="../shared-assets/images/equerreProfiles.png"
    shadow-intensity="1"
    camera-controls
    touch-action="pan-z"
    rotation="90 90 90">
</model-viewer>

Le problème est que nous ne pouvons pas fixer ce genre d'équerre avec le budget restant, par conséquence, nos profilés sont libres et n'ont pas une position fixe.
Nous avons donc décidé de concevoir notre propre [équerre](../conception/equerreProfile.html), nous pourrons la fixer en utilisant du matériel mis à notre disposition.

<style>
    #viewer
    {
        margin : auto;
        width : 500px;
        height : 500px;
    }
</style>

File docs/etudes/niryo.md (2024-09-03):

---
layout: default
nav_order: 2
title: Bras Robot Niryo
parent: Études et choix techniques
---
<script type="module" src="https://ajax.googleapis.com/ajax/libs/model-viewer/3.4.0/model-viewer.min.js"></script>

# Bras robotisé Niryo Ned 2 et ses accessoires

## Modèle 3D du bras robot Niryo Ned 2

<model-viewer
    id="viewer"
    alt="Modèle 3D du bras robot Niryo Ned 2"
    src="../shared-assets/models/Bras_Ned_2.gltf"
    poster="../shared-assets/images/capture_niryo.jpg"
    shadow-intensity="1"
    camera-controls
    touch-action="pan-z"
    rotation="90 90 90">
</model-viewer>

<style>
    #viewer
    {
        margin : auto;
        width : 500px;
        height : 500px;
    }
</style>

## Présentation

Le bras robot [Niryo Ned 2](https://niryo.com/fr/produits-cobots/ned-robot-collaboratif-six-axes/) est un cobot développé par la société [Niryo Robotics](https://niryo.com/fr/a-propos/).
Ce robot est accompagné de plusieurs composants. Nous aurons accès au convoyeur et le kit vision lié.

Premièrement, le convoyeur est un tapis roulant nous permettant de mouvoir des objets. Cet objet va nous servir a déplacer les objets et simuler une chaine de production a vitesse constante. De plus, la vitesse réglable du tapis peux nous permettre de varier les exercices.

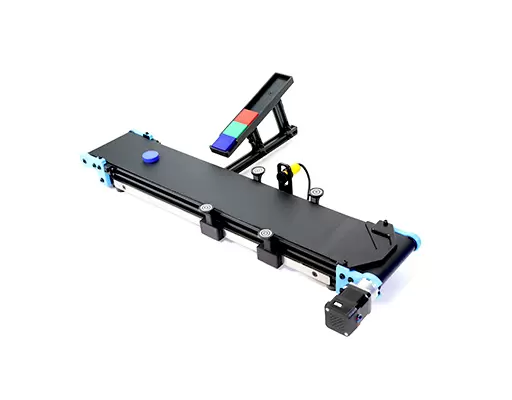
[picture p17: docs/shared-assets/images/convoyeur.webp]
Convoyeur

<style>
    img
    {
        width:100%;
    }
</style>
Source : [Convoyeur Niryo](https://niryo.com/fr/produits-cobots/tapis-roulant/)

Deuxièmement, le kit vision fourni est un capteur que l'on fixe au niveau de la tête du bras robotisé. Ce dernier permet la détection des formes et des couleurs et nécessite un unique branchement sur le bras Niryo pour fonctionner ce qui apporte aucun désagrément sur sa portabilité.

GIF représentant le kit vision
Source : GIF représentant le kit vision

L'intégralité de ces objets ont été commandé par UniLaSalle Amiens.

## Explication du choix

Ce robot présente de nombreux avantages.
Le premier étant le fait qu'il soit facile de le mettre en place ce qui réponds totalement à la problématique d'être utilisable sur des forums ou encore des présentations.
Le second avantage est le fait qu'il soit adaptables selon les besoins. En effet, ce robot accepte des mouvements selon 6 axes, possède une multitude de pinces différentes. Également, son kit vision nous permettra de développer des solutions éducatives poussées.
Le troisième avantage est sa conception pour l'utilisation en recherche, en enseignement ou en prototypage. L'enseignement étant notre priorité dans le projet ce bras répond totalement à nos attentes.

## Les accesoires fournis

Comme dit précédemment, nous avons à notre disposition des accessoires venant compléter les objets fournies par l'école UniLaSalle Amiens.

Tout d'abord, nous avons le convoyeur qui peux être connecté au robot comme être totalement indépendant. La première solution nous permet de mettre en rythme le robot et le convoyeur. Cette solution sera utile pour faire les différentes démonstrations. Avec cette dernière, nous n'accèdons uniquement à la vitesse et au sens du convoyeur.
La seconde solution pourra être utiliser lors de la présentation des différents équipements du pack. Elle peux également servir à être intégrer dans des systèmes plus important comme des maquettes utilisant plusieurs bras et plusieurs tapis. Dans ce cas de figure, nous n'avons pas d'autres options que dans le précédent cas.

Par la suite, nous disposons du kit vision. Ce coffrer est muni d'une caméra, de repères vision, d'un tapis vision et d'objets à saisir.
La caméra se positionne au niveau de la liaison entre la pince et le bras. Elle doit forcément être relié au bras robot pour fonctionner.
Les repères vision sont des cibles que l'on peux accrocher sur le convoyeur afin de mettre une zone dans laquelle le kit vision travaillera. Cela permet de ne pas créer de confusion avec les objets présents autour.
Le tapis vision, quant à lui, est une zone matérialisé par un support avec à chaque coins la même cible que sur les repères afin que le bras robot puisse l'utiliser comme espace de travail.

Pour finir, nous avons à disposition différentes pinces. Nous avons accès à des pinces classiques avec des différents angles d'ouvertures. Nous avons également un électro-aimant et une pompe à vide.

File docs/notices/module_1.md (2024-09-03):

---
layout: default
nav_order: 2
title: Module 1
parent: Notices
---

# Mise en place du module 1

## Explication du module

Ce module a pour but de trier selon les critères de formes ou de couleurs.

## Les étapes à suivre

1) Suivre les étapes de la notice « Mise en Place des Démonstrations »

2) Placer les plaques sur la grille comme sur les photos ci-dessous.

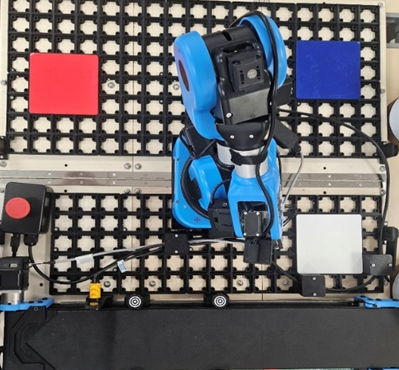
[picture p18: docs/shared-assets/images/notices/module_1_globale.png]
photos montrant le placement total

*placement globale*

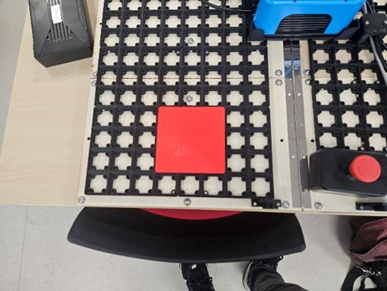
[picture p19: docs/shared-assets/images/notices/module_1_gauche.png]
photos montrant le placement du côté gauche

*placement gauche*

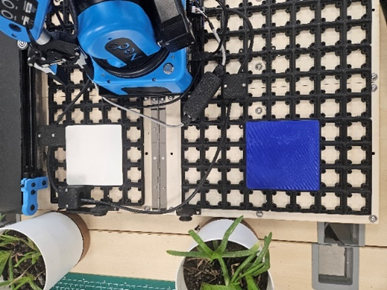
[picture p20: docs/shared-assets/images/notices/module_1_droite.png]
photos montrant le placement du côté droite

*placement droite*

3) Lancer l’ordinateur et le logiciel NiryoStudio.

4) Sélectionner dans la liste « mes derniers programmes » le programme voulu (uniquement les programmes commençant par « Module_1_VF ») et le lancer.

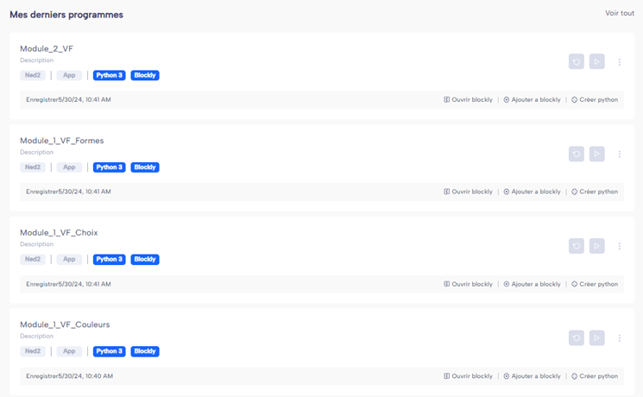
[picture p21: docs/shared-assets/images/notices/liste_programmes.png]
photos montrant la liste de programme


S’il n’apparaît pas, aller dans l’onglet « Blockly » présent dans la liste à gauche et appuyer sur le bouton « Ouvrir » en haut à droite. Puis sélectionner le programme voulu.

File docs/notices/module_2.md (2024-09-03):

---
layout: default
nav_order: 3
title: Module 2
parent: Notices
---

# Mise en place du module 2

## Explication du module

Ce module a pour but de récupérer un objet sur une position définie puis de l’amener à une autre position définie elle aussi.

## Les étapes à suivre

1) Suivre les étapes de la notice « Mise en Place des Démonstrations »

2) Placer les plaques sur la grille comme sur les photos ci-dessous (la couleur de la plaque n’est pas importante).

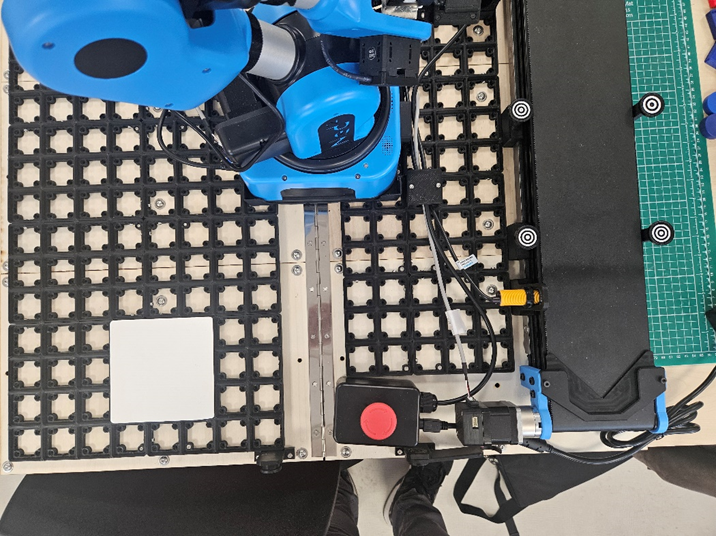
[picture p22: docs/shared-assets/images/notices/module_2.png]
photos montrant le placement total


3) Lancer l’ordinateur et le logiciel NiryoStudio.

4) Sélectionner dans la liste mes derniers programmes le programme Module_2_VF et le lancer.

photos montrant la liste de programme

S’il n’apparaît pas, aller dans l’onglet « Blockly » présent dans la liste à gauche et appuyer sur le bouton « Ouvrir » en haut à droite. Puis sélectionner le programme voulu.

5) Mettre les objets fournis (carré et rond de couleur) au centre de la plaque puis lancer le programme

**! Attention mettre les objets un par un. !**

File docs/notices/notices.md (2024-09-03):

---
layout: default
nav_order: 10
title: Notices
has_children: true
---

# Les différentes notices liées à l'installation du cobot et ses accessoires selon les modules voulus

- [Notice de mise en place globale](globale.md)
- [Notice de mise en place du module 1](module_1.md)
- [Notice de mise en place du module 2](module_2.md)

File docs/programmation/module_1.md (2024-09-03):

---
layout: default
title: Module tri avec kit vision
parent: Programmation
nav_order: 1
---

# Module de tri avec kit vision

Comme expliqué précédemment, le premier module est un module de tri. Ce tri sera fait par les couleurs et/ou par les formes.

## L'objectif

Ce module reproduit une chaîne de tri basique. Il trie donc les objets venant du convoyeur.

## Sa réalisation

Tout d'abord, ce module utilise le kit vision. Il faut donc le paramétrer. Pour ce faire, il est mis à disposition 4 cibles à fixer sur les côtés du convoyeur.
Une fois les cibles installer, il est nécessaire d'enregistrer leurs positions dans la mémoire du bras robot afin qu'il puisse les utiliser. C'est à ce moment qu'il faut utiliser la pointe de précision fourni dans le kit vision. 
Pour enregistrer chaque cible, il faut positionner la pointe au centre de cette dernière grâce au bouton "freemotion" sur le côté du bras. Une fois positionné, on appui sur le bouton "save" présent à côté du bouton précédent. On répète donc ces étapes pour les 3 autres cibles. 
Cette initialisation de la zone de travail est à faire à chaque fois qu'elle est déplacé à une nouvelle place mais plusieurs zones peuvent être paramétré dans le cobot.

Maintenant que cela est fait, il faut se concentrer sur le module en lui même.

Ce module se divise en plusieurs programmes.

Dans un premier temps,  choisi de mettre en place le tri par couleur. Pour ce faire, il faut articuler le bras robotisé afin que le kit vision puisse voir l'intégralité de la zone de travail choisi. Une fois bien positionné, la caméra scanne la zone en continu. Une fois qu'un objet y rentre, le cobot envoi la consigne de stopper le convoyeur. Par la suite, la caméra analyse l'objet (uniquement la couleur dans ce cas). Une fois l'analyse effectué, le cobot réagi en conséquence en saisissant l'objet puis en le déplacant à l'endroit prédéfini pour la couleur. Une fois l'objet déplacer, le convoyeur se remet en marche et le cobot se remet à sa position d'observation. Le programme se réexécute continuellement tant que la sécurité n'est pas atteinte. La sécurité est donc un compteur qui s'incrémente à chaque fois que le programme regarde dans la zone de travail et qu'il n'y a rien. Une fois arrivé à 50 (ce qui correspond à 15 secondes environ), le cobot reviens se mettre dans une position d'attente, le convoyeur s'arrête et le programme se termine. La valeur de la sécurité repasse à 0 à chaque fois que la caméra détecte un objet dans la zone de travail.

Une fois ce programme fonctionnel, il faut s'attaquer au code permettant le tri par forme. Pour ce faire, le même algorithme sera utiliser à l'exception que le cobot fait le choix en fonction de la forme et non de la couleur.

Les deux précédents tris ne permette pas de choisir un objet ou une couleur que l'utilisateur. Cela fais l'objet du troisième programme. Dans ce cas, il est demandé à l'utilisateur de choisir la couleur de leur choix (rouge par défaut) et sa forme (carré par défaut) afin de pouvoir sélectionner uniquement les objets de la couleur et de la forme choisi.
Dans ce cas, il existent deux positions de stockage des éléments triés. Le premier est celui où les objets souhaités seront déposés et le second comporte les objets ne correspondant pas au(x) critère(s).

Par la suite, il faut s'attaquer à la réalisation des ressources pédagogiques afin de permettre au élève de prendre en main facilement et rapidement le cobot Niryo Ned 2 tout en assurant la sécurité de chaque personne pouvant entrer en contact avec le robot collaboratif. Pour ce faire, il existe 2 types de codes pédagogiques.
La première proposition est un code à remmettre dans l'ordre où il y a tout les blocks de codes écrit mais divisé en plusieurs petits codes. L'objectif de cette ressource est de permettre aux élèves d'utiliser le cobot sans se préocupper de l'utilisation des systèmes de mouvements.
La seconde proposition est un code à remplir selon les envies de l'utilisateur. Pour ce faire, il sera fourni une architecture globale du code et les valeurs de déplacements seront laisser vides. Cela permettra aux élèves de se familiariser avec les déplacements du cobot et de leur effets.

Il est important de noter que des étapes positions intermédiaire ont été paramétré afin que le cobot ne rentre pas en collision avec d'autres objets pendant l'éxecution du programme.

**Une fois ces deux types d'exercices réaliser les élèves seront capable de faire leurs propres programmes basiques avec le cobot Niryo Ned 2, son convoyeur et son kit vision.**

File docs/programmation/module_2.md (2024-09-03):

---
layout: default
title: Module transfert
parent: Programmation
nav_order: 2
---

# Module de tri avec kit vision

Comme expliqué précédemment, le second module est un module de transfert sur le convoyeur

## L'objectif

Ce module viens donc chercher un objet à une position défini puis le deplace sur le début du convoyeur.

## Sa réalisation

Ce module se décompose en deux parties.

Le premier est la prise de l'objet. Pour la faire, il faut enregister la zone de récupération des objets. Il faut donc positionner le cobot à la position voulu grâce au bouton "freemotion" sur le côté du bras. Une fois positionné, on appui sur le bouton "save" pour récupérer la position dans notre programme.

Pour la seconde étape, il faut enregistrer la position à laquelle le cobot va déposer l'objet. On répète l'étape précedente mais en positionnant le bras robot à la nouvelle position voulu.

Une fois les deux position connu, il suffit de mettre une boucle qui fera les va-et-vient entre la position de ramassage de l'objet et la position de dépôt.
Il faut tout de même faire attention que la trajectoire du cobot ne vienne pas renconter d'autres objets placés.

Par la suite, il faut s'attaquer à la réalisation des ressources pédagogiques afin de permettre au élève de prendre en main facilement et rapidement le robot tout en assurant la sécurité de chaque personne pouvant entrer en contact avec le robot. Pour ce faire, il existe 2 types de codes pédagogiques.
La première proposition est un code à remmettre dans l'ordre où il y a tout les blocks de codes écrit mais divisé en plusieurs petits codes. L'objectif de cette ressource est de permettre aux élèves d'utiliser le robot sans se préocupper de l'utilisation des systèmes de mouvements.
La seconde proposition est un code à remplir selon les envies de l'utilisateur. Pour ce faire, il sera fourni une architecture globale du code et les valeurs de déplacements seront laisser vides. Cela permettra aux élèves de se familiariser avec les déplacements du robot et de leur effets.

Il est important de noter que des étapes positions intermédiaire ont été paramétré afin que le cobot ne rentre pas en collision avec d'autres objets pendant l'éxecution du programme.

**Une fois ces deux types d'exercices réaliser les élèves seront capable de faire leurs propres programmes basiques avec le cobot et son convoyeur.**

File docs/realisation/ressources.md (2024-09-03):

---
layout: default
title: Choix des ressources
parent: Réalisation
nav_order: 1
---

# Choix des différentes ressources

Pour réaliser notre mallette, nous avons étudier les différents matériaux possibles pour sa fabrication.
Nous avons dû étudier les caractéristiques de chaque famille de matériaux ainsi que les différences entre les matériaux de même catégorie.

## Liste des familles de matériaux

| Plastiques | Bois | Métaux |
| :---: | :---: | :---: |
| Polypropylène | Peuplier | Aluminium |
| Polyéthylène  | Bouleau  | Acier inoxydable|
| Polycarbonate | Okoumé | |

Les matériaux retenus sont les suivants : le Polypropylène, le Peuplier ainsi que l'Aluminium.

### Caractéristiques de chaque matériau

| | Polypropylène |  Peuplier |  Aluminium  |
| :---: | :---: | :---: | :---: |
| Étanchéité  | ✓ | ✗ | ✓ |
| Poids | [946 kg/m3](https://blogue.polyalto.com/les-plastiques-sont-ils-legers#:~:text=Polypropylène%20%3A%20946%20kg%2Fm3) | [410 kg/m3](https://www.leroymerlin.fr/produits/menuiserie/panneau-planche-et-materiaux-bois/panneau-bois-agglomere-mdf/panneau-bois-recoupable/panneau-contreplaque-peuplier-ep-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) | [2 700 kg/m3](https://blogue.polyalto.com/les-plastiques-sont-ils-legers#:~:text=Aluminium%20%3A%202700%20kg%2Fm3) |
| Sensibilité |  Chaleur / UV |  Humidité | Rayures |  
| Coût |  [68 €/m2](https://www.polydis.fr/pp-extrude-gris-7032-2000x1000-mm-c2x40088463) |  [33 €/m2](https://www.leroymerlin.fr/produits/menuiserie/panneau-planche-et-materiaux-bois/panneau-bois-agglomere-mdf/panneau-bois-recoupable/panneau-contreplaque-peuplier-ep-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) | [530 €/m2](https://fr.rs-online.com/web/p/feuilles-metalliques/7781661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) |

## Choix final

Le matériau que l'on va utiliser pour réaliser notre malette est le **peuplier**, on va utiliser des plaques en contreplaqué de 5mm.

---

## Choix des systèmes d'accroche

### Les profilés

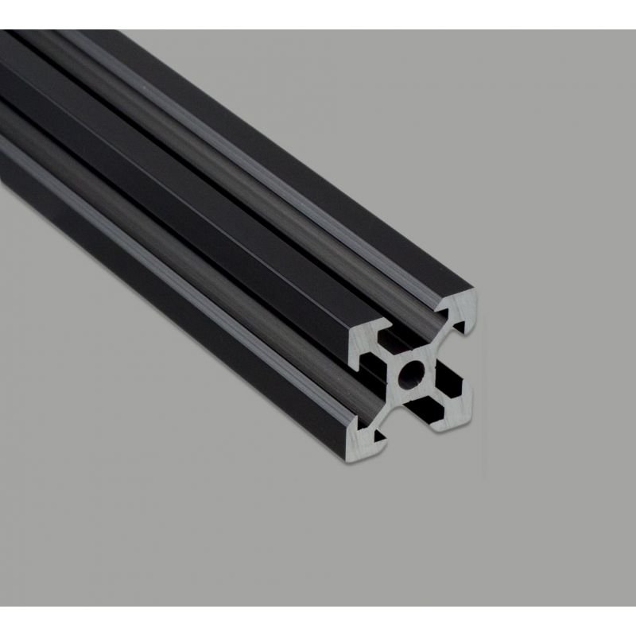
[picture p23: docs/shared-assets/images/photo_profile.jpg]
photo profilés


Les profilés seront utilisés pour créer un renfort pour le socle de la boîte, cela évitera de devoir doubler l'épaisseur de contreplaqué pour pouvoir supporter tout le poids qui sera contenu dans la boîte.

### Les sauterelles

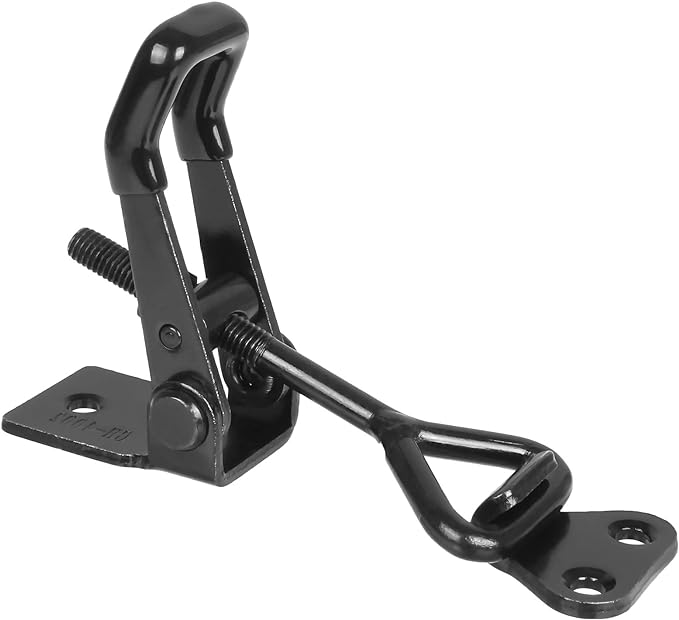
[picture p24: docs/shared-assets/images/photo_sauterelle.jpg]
photo sauterelles


Nous utiliserons ce type de sauterelles pour fermer notre mallette. Simple et robuste, ce système permet une ouverture/fermeture rapide, de plus elles sont bloquantes.
Elles serviront à maintenir le couvercle de la mallette avec le socle.

### La charnière

photo charnière

Nous utiliserons une charnière piano sur la longueur du socle, ce qui permettra aux deux parties qui le compose de pouvoir se déplier et se transformer en zone de travail.
De plus, elle offrira un renfort au niveau de l'arête pour les futures manipulations et transport de la mallette.

### Les équerres

photo équerre

Les équerres seront utilisées pour la fabrication du couvercle de la mallette.
Elles permettront de renforcer les angles et d'assembler proprement les différentes plaques de contreplaqué ensemble.

### Colle & Vis

Pour fixer les plaques de bois entre elles, nous avons décidé d'utilisé de la colle.
C'est facile d'utilisation et c'est résistant.
Ensuite pour les différents accessoires précédemment cités, nous allons devoir les visser et pour ce faire, nous allons utiliser des vis M3.

---

## Le Vernis

photo vernis

Le vernis que nous utiliserons est un vernis marin.
Ce vernis à la particularité de rendre le bois étanche ce qui permettra de protéger la mallette de l'eau.

<style>
    img{
        width: 300px;
        height: auto;
        display: block;
    }
</style>

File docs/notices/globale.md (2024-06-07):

---
layout: default
nav_order: 1
title: Globale
parent: Notices
---

# Mise en place globale

1. Déplier la mallette ainsi que prendre les différents accessoires nécessaires à la démonstration (voir l’étape 2 de la fiche liée à la démonstration voulu)

2. Il faut placer le robot (comme sur la photo ci-dessous) et les équipements utiles (cf. fiche liée à la démonstration).

photos montrant le placement du cobot

3) Alimenter le cobot avec le câble prévu à cet effet. Ne pas oublier de mettre en place le bouton d’arrêt d’urgence.

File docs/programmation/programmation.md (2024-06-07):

---
layout: default
title: Programmation
nav_order: 8
has_children: true
---

# Programmation

## Sommaire des Modules

Le processus de programmation est divisé en plusieurs parties clés :

1. [Module chaîne de tri](module_1.md)
2. [Module de transfert de pièce](module_2.md)

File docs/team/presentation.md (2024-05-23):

---
layout: default
title: Présentation de l'équipe
nav_order: 2
---

# Présentation de l'équipe
<style>
.grid-container {
    display: grid;
    grid-template-columns: auto auto auto auto;
    gap: 20px;
    text-align: center; /* Pour centrer le texte sous les images */
}

img {
    
}

.rounded-image {
    border-radius: 50%;
    width: 150px; /* Taille des images */
    height: auto;
}

.image-caption {
    margin-top: 5px; /* Espacement entre l'image et le texte */
}
</style>

<div class="grid-container">
    <div>
        Photo Benjamin
        <p class="image-caption">Benjamin BONHOMME</p>
    </div>
    <div>
        Photo Jules
        <p class="image-caption">Jules MARGOLLÉ</p>
    </div>
    <div>
        Photo Alexis
        <p class="image-caption">Alexis PINOTEAUX</p>
    </div>
    <div>
        Photo Yohann
        <p class="image-caption">Yohann VERGNIOLE</p>
    </div>
</div>
Nous sommes tous les quatre étudiants à UniLaSalle Amiens en 3e année d'études d'ingénierie.
Durant cette année, nous devons réaliser un projet de groupe, le nôtre sera la conception d'une mallette de rangement pour un Cobot et ses accessoires ainsi qu'à la réalisation de programme pédagogique de son fonctionnement.

|| Programmation | Modélisation | Bricolage |
|:-:|:--:|:---:|:--:|
| Benjamin BONHOMME | 3 | 5 | 3 |
| Jules MARGOLLÉ | 5 | 5 | 3 |
| Alexis PINOTEAUX | 5 | 3 | 4 |
| Yohann VERGNIOLE | 5 | 3 | 4 |

### Attribution des rôles
- Benjamin est en charge de la modélisation 3D des accessoires de la mallette
- Jules est en charge de la modélisation 3D de la mallette
- Alexis est en charge de la gestion des matériaux et des commandes 
- Yohann est en charge de la programmation du Cobot

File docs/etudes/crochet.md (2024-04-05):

---
layout: default
nav_order: 6
title: Butée (fixation)
parent: Études et choix techniques
---

# Fixation / Butée pour la fermeture de la malette

Nous avons, après avoir choisi le type de malette, réfléchi à quels types de fixation nous pouvions utiliser afin de faciliter le déploiement la malette et sa fermeture.

## Tentative n°1

Illustration crochet tentative n°1

Notre crochet était malheureusement trop long pour qu'il puisse se glisser sur le support que l'on peut voir sur l'image ci-dessus.
De plus, certaines liaisons n'ont pas été parfaitement dimensionées, nous avonc dû ajuster le tir sur la 2ème tentative afin d'obtenir un glissement parfait et un bon maintient des cotés de la malette lors de sa fermeture par le biais des crochets.

## Tentative n°2(finale)

Illustration crochet tentative finale

Sur cette itération finale, nous avons pris la décision de faire un crochet allongé avec un creux parralèle à la plaque inférieure de la malette afin de faciliter l'emboitement des deux pièces tout en s'assurant du maintien de la plaque latérale.

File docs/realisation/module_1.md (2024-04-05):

---
layout: default
title: Choix des matériaux
parent: Réalisation
nav_order: 10
---

# Module de tri avec kit vision

Comme dit [plus haut](../applications/chaineTri.md), notre premier module est un module de tri. Ce tri sera fait par les couleurs et/ou par les formes.

## L'objectif

Dans ce module nous cherchons à reproduire une chaîne de tri basique. Nous cherchons donc à trier les objets venant du convoyeur.

## Sa réalisation

Tout d'abord, ce module utilise le kit vision. Il faut donc le paramétrer. Pour ce faire nous avons à disposition 4 cibles à fixer sur les côté du convoyeur. 
Une fois les cibles installer, il est nécessaire d'enregistrer leurs positions dans le robot afin qu'il puisse les utiliser. C'est à ce moment que nous devons utiliser la pointe de précision. 
Nous venons positionner la pointe au centre de la cible grâce au bouton "freemotion" sur le côté du bras. Une fois positionner, on appui sur le bouton "save" présent à la gauche du bouton précédent. On répète donc ces étapes pour les 3 autres cibles. 
Cette initialisation de la zone de travail est à faire à chaque fois que nous la déplacons à une nouvelle place mais plusieurs zone peuvent être paramétrer dans le robot. 

Ensuite nous allons pouvoir nous concentrer sur le module en lui même. 

Ce module se divise en plusieurs programmes. 

Dans un premier temps, nous avons choisi de mettre en place le tri par couleur. Pour ce faire, nous placons le robot afin que le kit vision puisse voir l'intégralité de la zone de travail choisi. Une fois bien positionné nous choisissons de scanner en continu la zone. Une fois qu'un objet y rentre, nous stoppons le convoyeur. Par la suite, le robot analyse l'objet (uniquement la couleur dans ce cas). Une fois l'analyse effectué, le robot réagi en conséquence en saisissant l'objet puis en le déplacant à l'endroit prédéfini pour la couleur. Une fois l'objet déplacer, le convoyeur se remet en marche et le robot reviens se mettre à sa position d'observation. Le programme se réexécute continuellement tant que la sécurité n'est pas atteinte. La sécurité est donc un compteur qui s'incrémente à chaque fois que le programme regarde dans la zone de travail et qu'il n'y a rien. Une fois arrivé à 50 le robot reviens se mettre dans une position d'attente, le convoyeur s'arrête et le programme se termine. La valeur de la sécurité repasse à 0 à chaque fois que la caméra détecte un objet dans la zone de travail.

Une fois ce programme fonctionnel, nous décidons de s'attaquer au code permettant le tri par forme. Nous utilisons le même algorithme à l'execption que le robot fait le choix en fonction de la couleur et non de la forme.

Les deux précédents tris ne nous permette pas de choisir un objet ou une couleur que nous souhaitons. Cela fais l'objet du troisième programme. Dans ce cas, nous demandons à l'utilisateur de choisir la couleur de leur choix (rouge par défaut) et sa forme (carré par défaut) afin de pouvoir sélectionner uniquement les objets de la couleur et de la forme choisi.
Dans ce cas, nous avons deux positions de stockage des éléments triés. Le premier est celui où nous avons les objets souhaités et le second comporte les objets necorrespondant pas au(x) critère(s).

Par la suite, nous nous devons de réaliser des ressources pédagiques afin de permettre au élève de prendre en main facilement et rapidement le robot tout en assurant la sécurité de chaque personne pouvant entrer en contact avec le robot. Pour ce faire, nous proposons 2 types de codes pédagogiques. 
La première proposition est un code à remmettre dans l'ordre où il y a tout les blocks de codes écrit mais divisé en plusieurs petits codes. L'objectifs de cette ressource est de permettre aux élèves d'utiliser le robot sans se préocupper de l'utilisation des systèmes de mouvements. 
La seconde proposition est un code à remplir selon les envies de l'utilisateur. Pour ce faire, nous allons fournir architecture globale du code et laisser vide les valeurs de déplacements. Cela permettra aux élèves de se familiariser avec les déplacements du robot et de leur effets. 

**Une fois ces deux types d'exercices réaliser les élèves seront capable de faire leur propre programme basique avec le robot, son convoyeur et son kit vision.**

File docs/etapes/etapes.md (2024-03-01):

---
layout: default
title: Etapes de fabrication
nav_order: 7
has_children: true
---

# Étapes de Fabrication

Bienvenue dans la section dédiée aux étapes de fabrication du projet XYZ. Ici, vous trouverez des guides détaillés pour chaque étape du processus de fabrication.

## Aperçu des Étapes

Le processus de fabrication est divisé en plusieurs étapes clés :

1. [Préparation des Matériaux](etape_1)
2. [Assemblage](etape_2)
3. [Finition]()
4. [Contrôle Qualité]()

## Commencer

Pour commencer, assurez-vous de bien comprendre chaque étape et de disposer de tous les outils et matériaux nécessaires. Suivez les étapes dans l'ordre pour garantir la qualité et l'efficacité du processus de fabrication.

---

Pour toute question ou aide supplémentaire, n'hésitez pas à contacter notre équipe.

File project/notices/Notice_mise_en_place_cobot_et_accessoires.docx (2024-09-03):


Mise en Place des Démonstrations

1) Déplier la mallette ainsi que prendre les différents accessoires nécessaires à la démonstration (voir l’étape 2 de la fiche liée à la démonstration voulu)

2) Il faut placer le robot (comme sur la photo ci-dessous) et les équipements utiles (cf. fiche liée à la démonstration).


3) Alimenter le cobot avec le câble prévu à cet effet. Ne pas oublier de mettre en place le bouton d’arrêt d’urgence.

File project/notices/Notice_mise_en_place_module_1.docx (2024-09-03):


Mise en Place Module 1

Explication du module :

Ce module a pour but de trier selon les critères de formes ou de couleurs.

Les étapes à suivre :

1) Suivre les étapes de la notice « Mise en Place des Démonstrations »

2) Placer les plaques sur la grille comme sur les photos ci-dessous.


Placement Globale

Placement Côté Gauche

Placement Côté Droit

3) Lancer l’ordinateur et le logiciel NiryoStudio.

4) Sélectionner dans la liste « mes derniers programmes » le programme voulu (uniquement les programmes commençant par « Module_1_VF ») et le lancer.


S’il n’apparaît pas, aller dans l’onglet « Blockly » présent dans la liste à gauche et appuyer sur le bouton « Ouvrir » en haut à droite. Puis sélectionner le programme voulu.

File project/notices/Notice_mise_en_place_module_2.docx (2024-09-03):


Mise en Place Module 2

Explication du module :

Ce module a pour but de récupérer un objet sur une position définie puis de l’amener à une autre position définie elle aussi.

Les étapes à suivre :

1) Suivre les étapes de la notice « Mise en Place des Démonstrations »

2) Placer les plaques sur la grille comme sur les photos ci-dessous (la couleur de la plaque n’est pas importante).


3) Lancer l’ordinateur et le logiciel NiryoStudio.

4) Sélectionner dans la liste mes derniers programmes le programme Module_2_VF et le lancer.


S’il n’apparaît pas, il faut aller dans l’onglet « Blockly » présent dans la liste à gauche et appuyer sur le bouton « Ouvrir » en haut à droite. Puis sélectionner le programme voulu.

5) Mettre les objets fournis (carré et rond de couleur) au centre de la plaque puis lancer le programme

! Attention il faut mettre les objets un par un. !

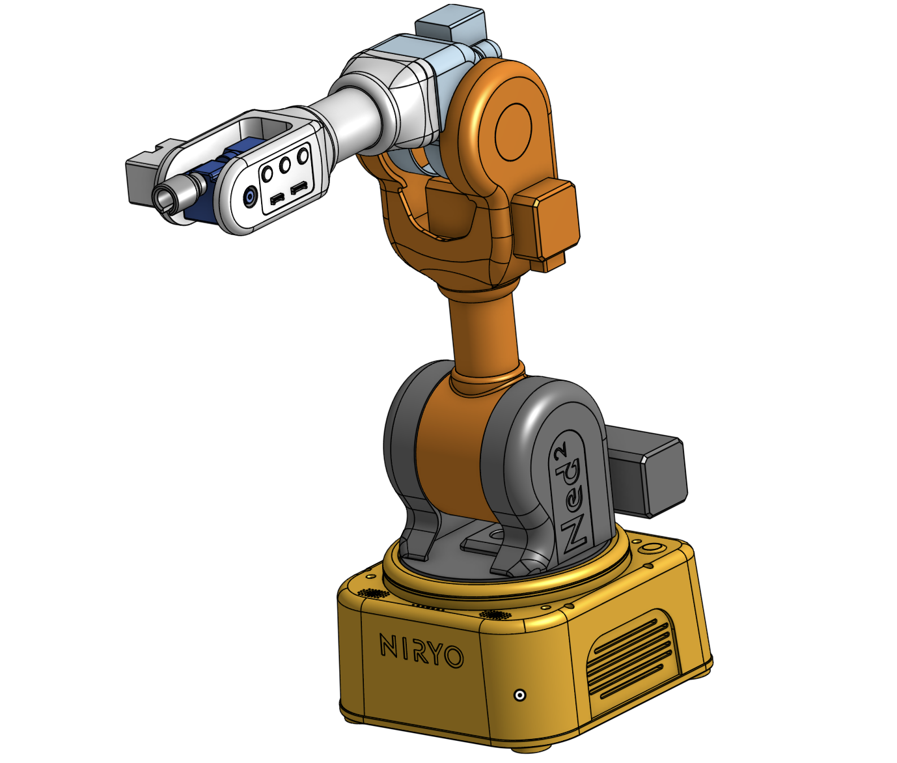
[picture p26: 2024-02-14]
docs/shared-assets/images/capture_niryo.png

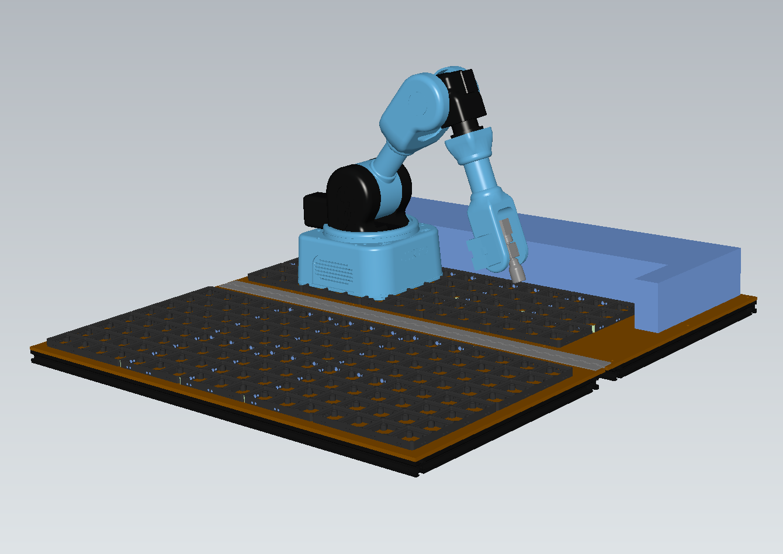
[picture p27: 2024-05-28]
docs/shared-assets/images/3D_REPRESENTATION.png

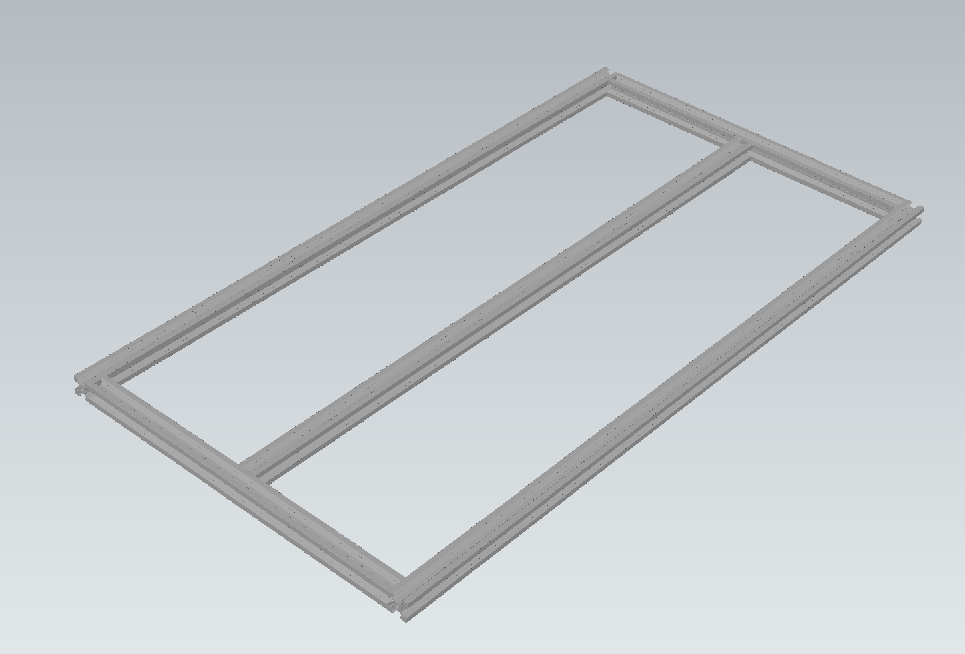
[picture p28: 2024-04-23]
docs/shared-assets/images/capture_armature.png

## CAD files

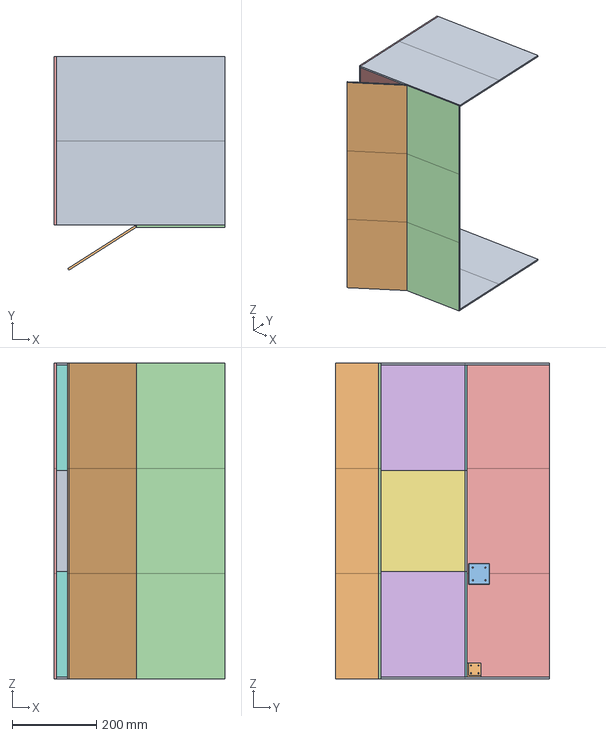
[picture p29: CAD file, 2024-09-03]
project/3DModels/Couvercle boite.step
405.0 x 507.1 x 750.0 mm

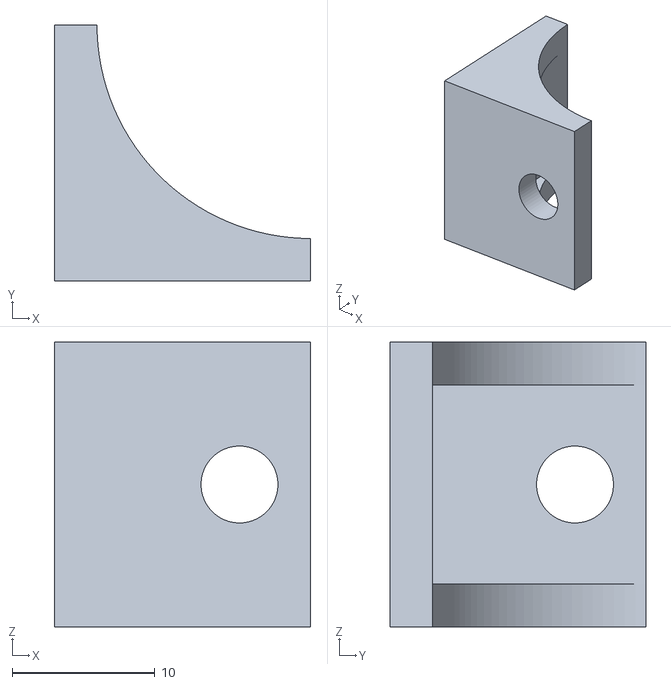
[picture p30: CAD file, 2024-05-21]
project/3DModels/equerreFixe.stl
18.0 x 18.0 x 20.0

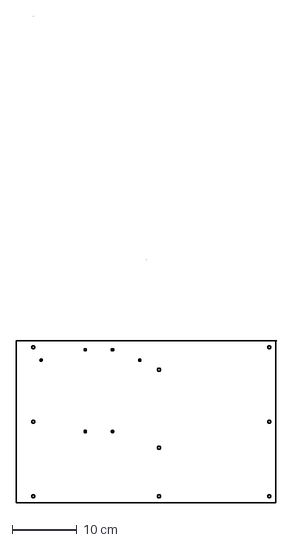
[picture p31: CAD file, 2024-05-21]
project/3DModels/plaqueBaseBas v.dxf
40.2 x 75.0 cm

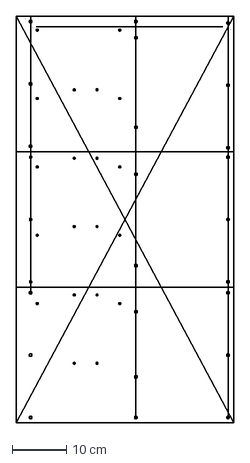
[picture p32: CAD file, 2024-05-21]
project/3DModels/plaqueBaseMilieu.dxf
40.0 x 75.0 cm

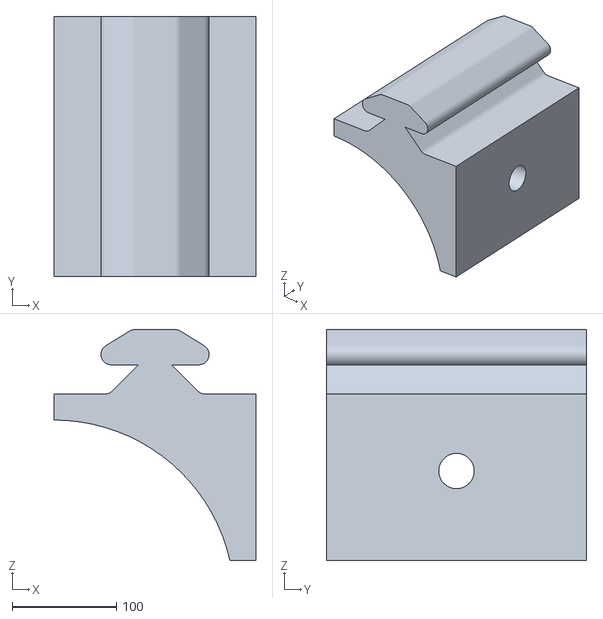
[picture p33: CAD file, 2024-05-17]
project/3DModels/soutien_charnière_profile.stl
194.0 x 250.0 x 222.0

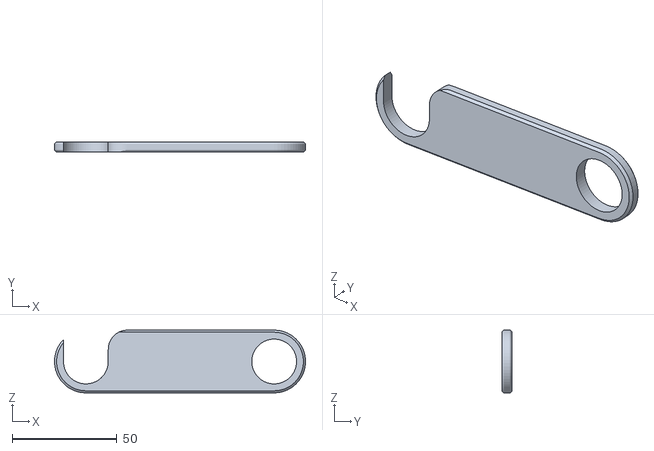
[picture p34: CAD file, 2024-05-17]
project/3DModels/support_crochet.stl
120.0 x 5.00 x 30.0

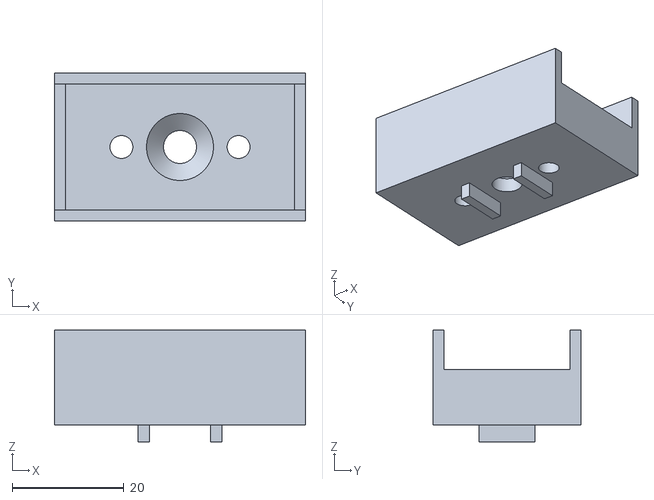
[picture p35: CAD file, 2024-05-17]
project/3DModels/reparation_aimant_T_de_fixation.stl
45.0 x 26.5 x 20.0

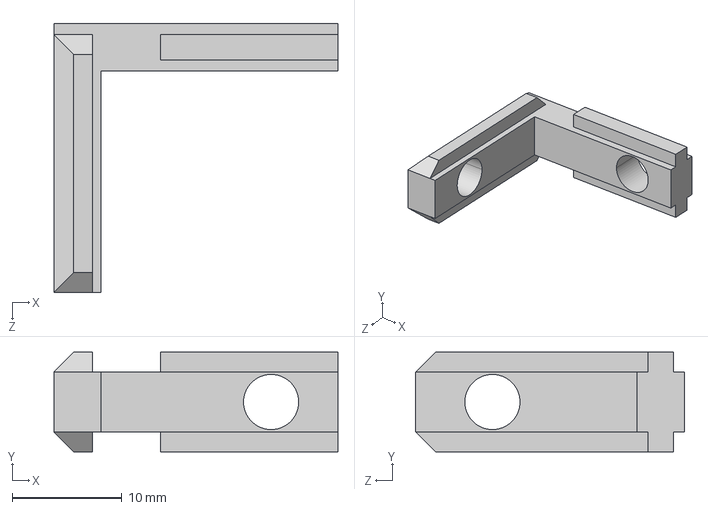
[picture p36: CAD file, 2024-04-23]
project/3DModels/equerreProfiles.STEP
25.9 x 9.10 x 24.5 mm

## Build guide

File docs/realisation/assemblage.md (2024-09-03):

---
layout: default
title: Assemblage
parent: Réalisation
nav_order: 2
---

# Assemblage

Nous allons désormais passer à l'assemblage de nos différents éléments.

## Armature du socle

Ci-dessous vous trouverez une vidéo de la fixation de l'armature du socle à laquelle on va venir ajouter les plaques en contreplaqués de 5mm.

<video width="600" controls>
  <source src="../shared-assets/video/video_armature.mp4" type="video/mp4">
</video>

## Fixation de la grille et des systèmes d'accroche

Une fois l'armature et les plaques en bois fixées ensemble, nous avons ajouté la grille modulaire ainsi que les systèmes d'accroche pour maintenir le socle en place pour le fixer au couvercle.
Mais avant cela nous allons ajouter le convoyeur et le cobot.

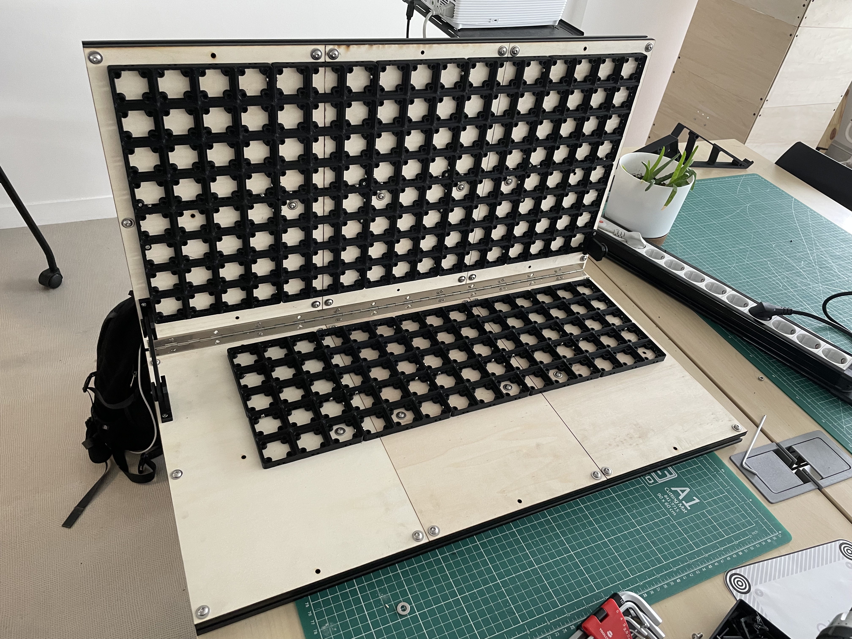
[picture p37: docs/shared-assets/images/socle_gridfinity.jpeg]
socle gridfinity


## Fixation du convoyeur et ajout du cobot

Le convoyeur est fixé lui aussi aux plaques en bois, quant au cobot il est posé sur un support qui vient s'emboîter sur la grille à l'emplacement de son choix.

socle gridfinity

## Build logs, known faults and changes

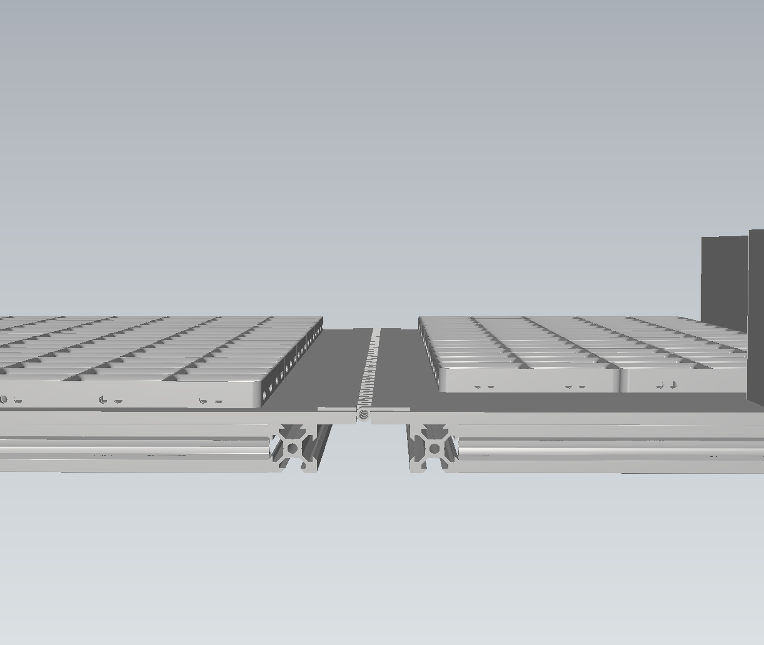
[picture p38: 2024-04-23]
docs/shared-assets/images/problemeCharniere.png

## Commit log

2024-03-20 Create prototypes mallette
2024-03-20 ajout des accessoires
2024-04-05 Ajout présentation de l'équipe
2024-04-05 Ajout des ressources
2024-04-19 Ajout du prototype réalisé pour la malette 3
2024-06-07 ajout des programmes
2024-06-11 ajout passage de câbles
2024-06-11 Correction des fautes
2024-06-11 Ajout du fichier du couvercle
    [Couvercle boite.step]
